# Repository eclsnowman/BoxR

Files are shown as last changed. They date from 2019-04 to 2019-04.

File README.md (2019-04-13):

# BoxR
BoxR 3D Printer by SMW3D aka Hobby-Fab (with Eric Lien)

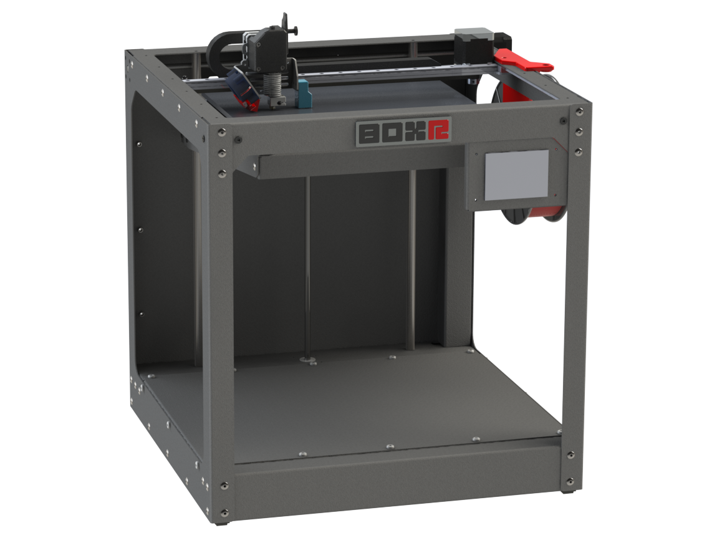
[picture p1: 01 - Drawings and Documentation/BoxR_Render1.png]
BoxR-3DP Render Image1


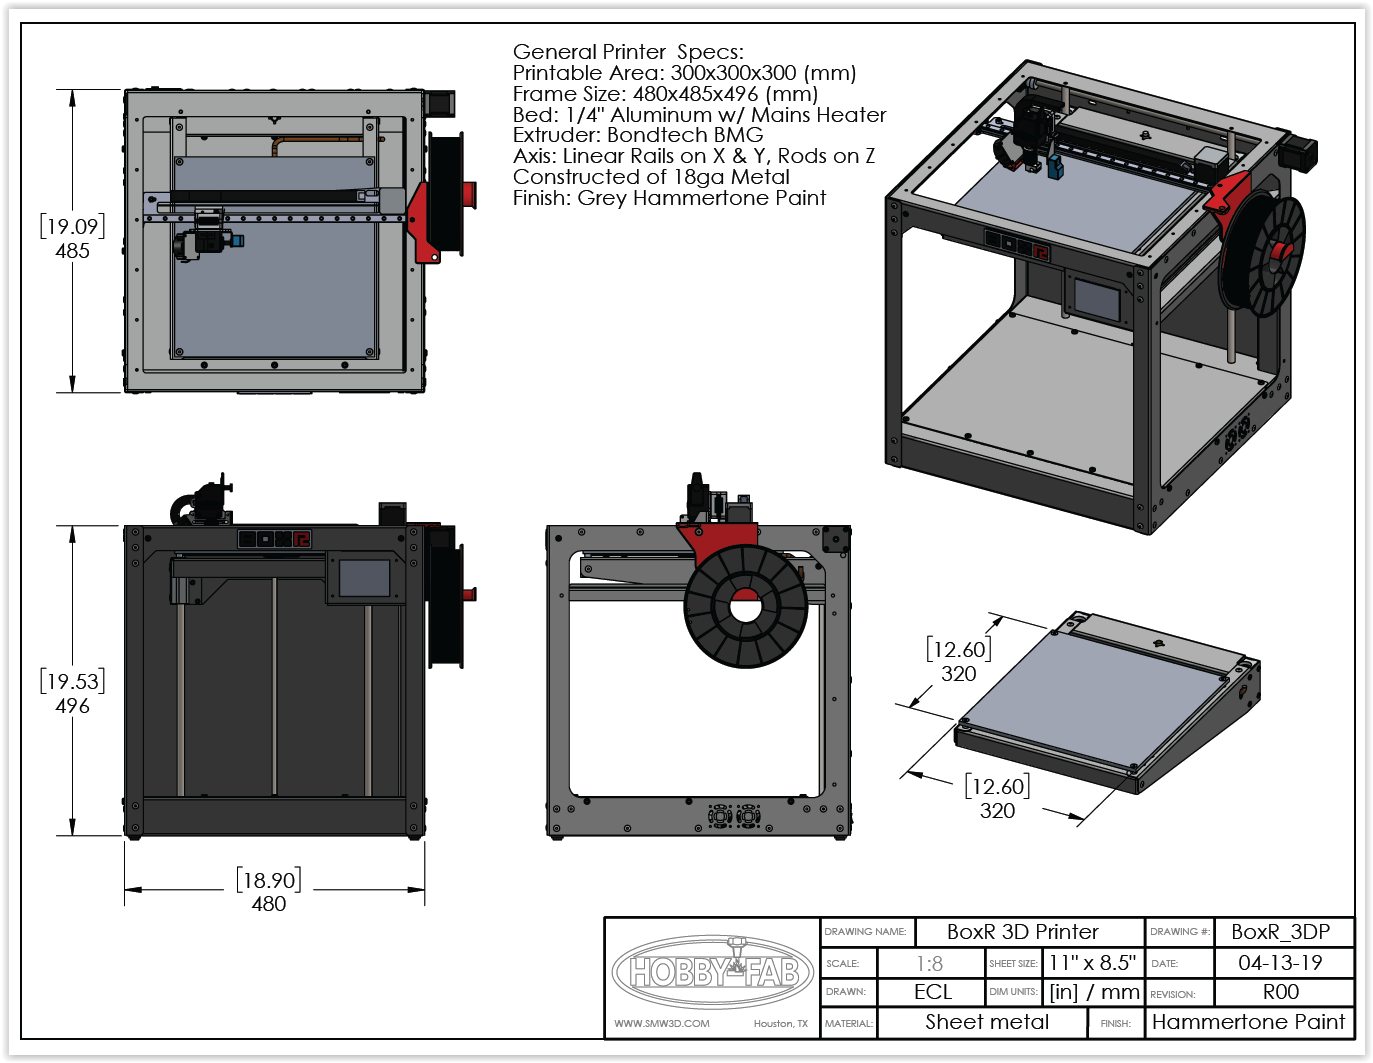
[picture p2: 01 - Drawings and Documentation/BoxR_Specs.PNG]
BoxR-3DP Specs


The BoxR 3D Printer is a larger format (300mm x 300mm x 300mm) cartesian x/y gantry printer with a moving z-axis bed. The BoxR printer was a project that Brandon Satterfield and I worked on together. Originally it was intended as a possible product line he could sell under his SMW3D / Hobby-Fab business. I have had the pleasure of knowing Brandon Satterfield for many years through the now defunct Google+. Over those years I have been fortunate enough to work on several cool project with Brandon and the team at SMW3D. Alas the advent of the CR-10, Ender3, and similar low cost reasonable quality Chinese printers that put the skids on this project. There are only two of these printers currently in the wild. I have one, and Brandon Satterfield has the other. Perhaps you might be the next?

On a sad note: due to the Chinese market spurring the race to the bottom on maker parts, kits, and printers it drove Brandon and his team on to greener pastures with the closure of Hobbyfab in 2019. But I am delighted to announce that Brandon has given me the OK to release the designs and plans on many of the cool machines we developed together out here on Github. The files here are my best attempt to cleanup and document with detailed 3D models the BoxR 3D printer as we left off on the project. I still use my BoxR Printer regularly, and actually had it out at MRRF the last few years. It is a capable and reliable 3D printer. If you have interest in building one, all the details to get you started should be available in this Github.

I have the 3D model files saved in several formats. I work in Solidworks natively, but I have also exported the model into Fusion360, X_T, Step, 3D-PDF. In addition I have generated DXF files for the 2D Panels which could be formed at a local sheet metal fabrication house by a potential maker looking to replicate the design. The BoxR design was my first for endeavor into sheet metal modeling in Solidworks. I have since improved my skills in this area, but I feel it is not too bad for a first attempt :)

I would like to end this by saying Brandon and his group over the years did amazing work for the community. They sponsored projects to many makers via at cost or free components to develop cool projects. They were always available to answer questions to potential makers on the kits and projects they sold (day or night). The maker community lost something special with the closure of SMW3D/Hobby-Fab. But the impact they left on the maker community will live on.

Thank you Brandon and team. You are amazing. And I am glad to have been but a small part in your chapter of the Maker Revolution story.

-Eric Lien

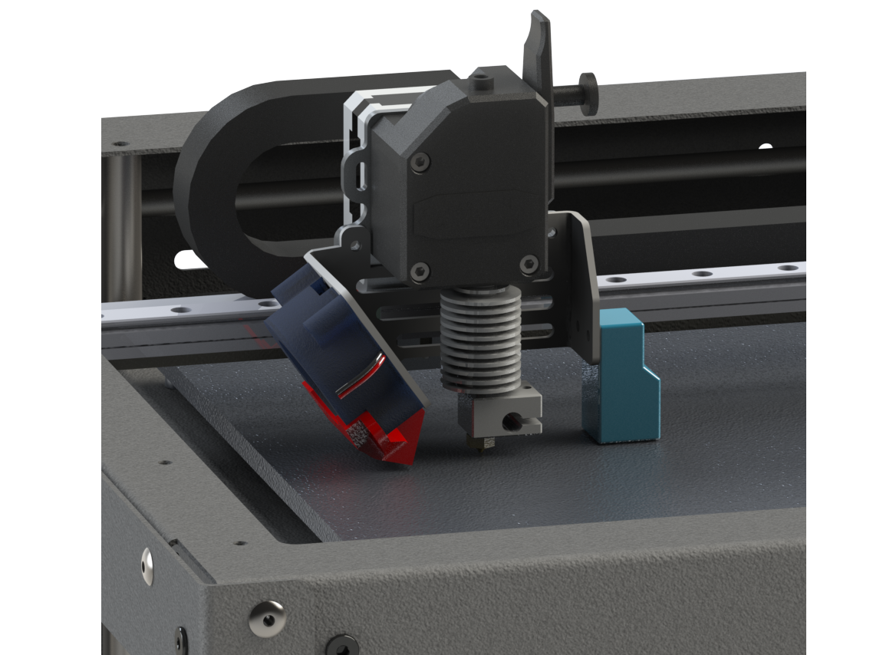
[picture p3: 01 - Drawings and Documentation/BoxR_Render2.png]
BoxR-3DP Render Image2


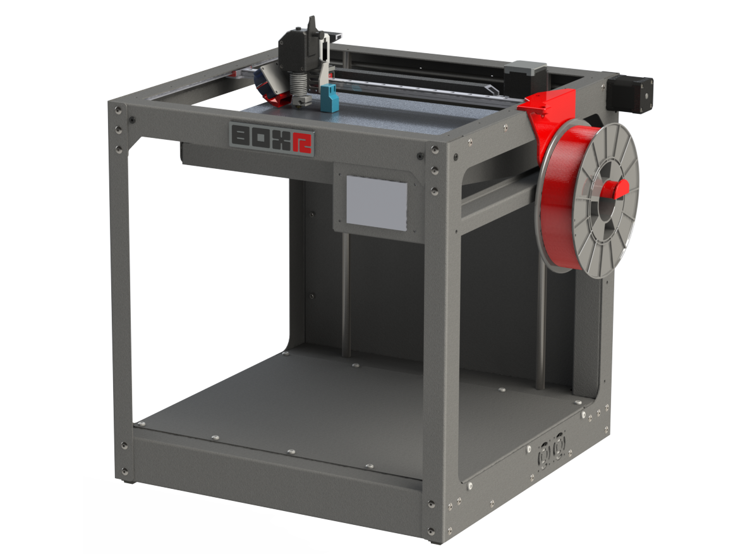
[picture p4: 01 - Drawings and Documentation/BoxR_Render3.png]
BoxR-3DP Render Image3


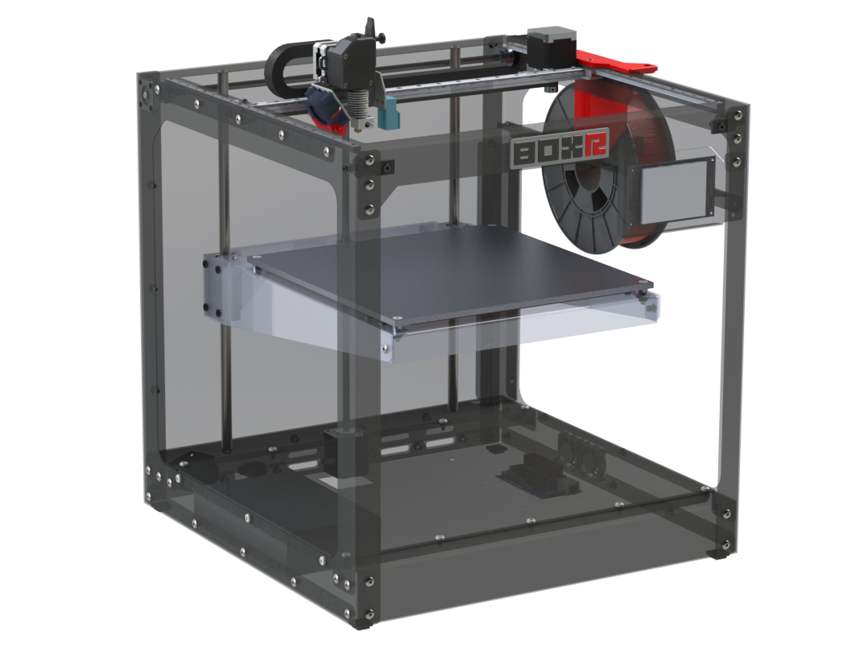
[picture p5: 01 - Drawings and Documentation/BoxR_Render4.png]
BoxR-3DP Render Image4


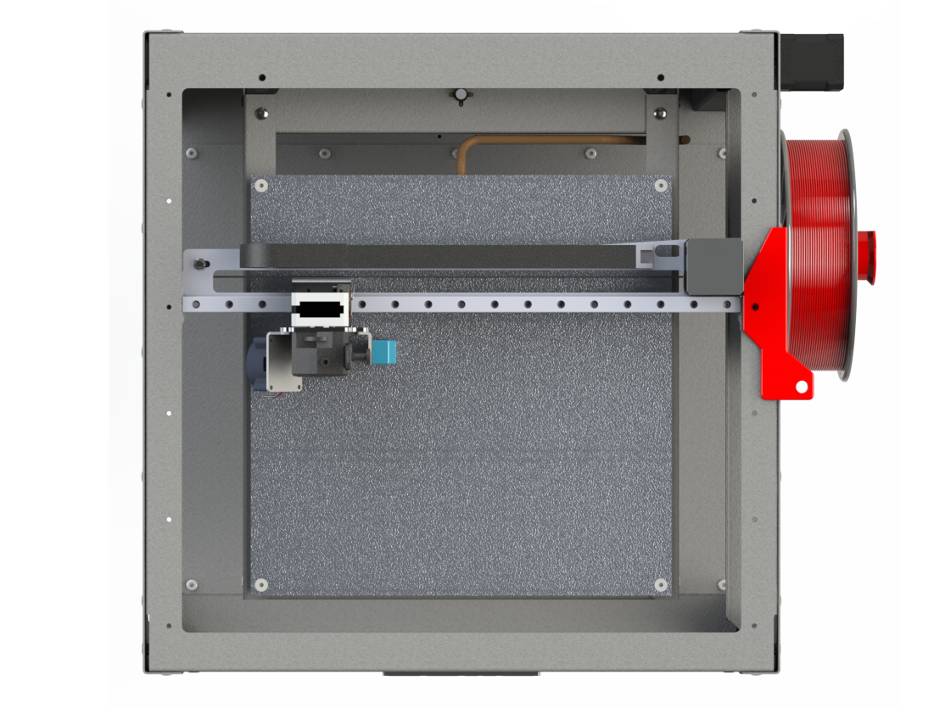
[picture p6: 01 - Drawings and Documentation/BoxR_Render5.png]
BoxR-3DP Render Image5


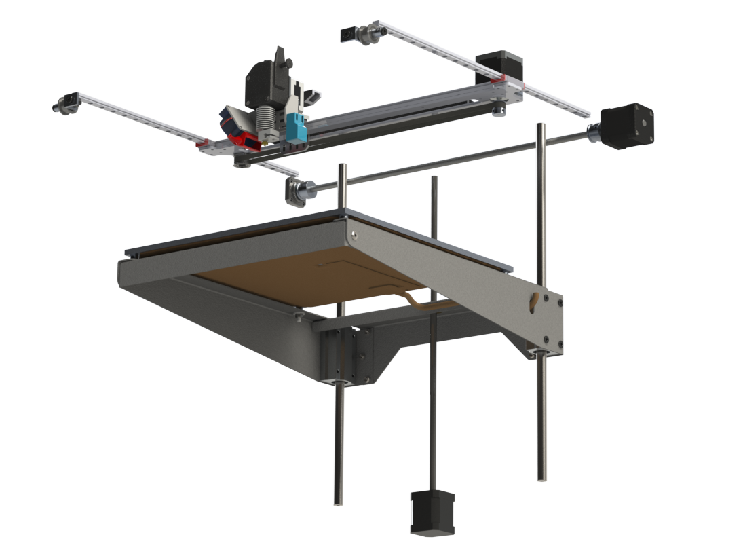
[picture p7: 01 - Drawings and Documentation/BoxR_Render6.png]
BoxR-3DP Render Image6


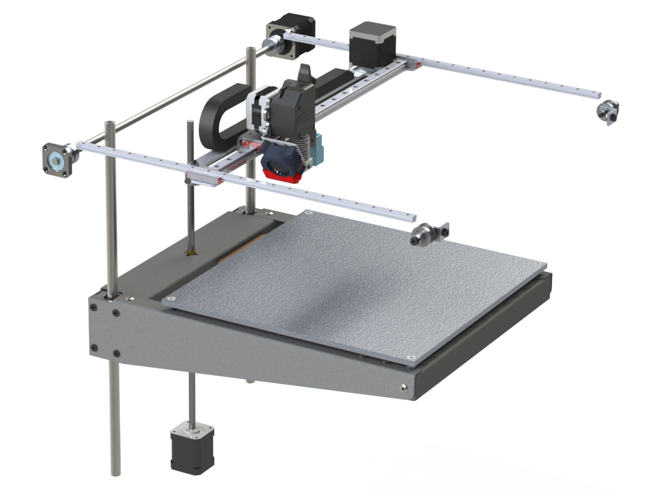
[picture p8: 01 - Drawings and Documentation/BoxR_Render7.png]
BoxR-3DP Render Image7


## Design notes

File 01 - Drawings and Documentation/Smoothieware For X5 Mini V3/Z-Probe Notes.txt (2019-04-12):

Okay so in the smoothieware docs on zprobes it states that a zprobe is not an endstop and cannot be used to home the z axis. But it can.

So I defined it as follows:
gamma_min_endstop                            1.29!^            #
#gamma_max_endstop                           1.28!^            #
gamma_homing_direction                       home_to_min       #
gamma_min                                    0                #
gamma_max                                    183              #

#probe endstop
#probe_pin                                   1.29!^            # optional pin for probe

# optional Z probe
zprobe.enable                                true           # set to true to enable a zprobe
zprobe.probe_pin                             1.29!^          # pin probe is attached to if NC remove the !
zprobe.slow_feedrate                         10               # mm/sec probe feed rate
zprobe.debounce_ms                           1             # set if noisy
zprobe.fast_feedrate                         100             # move feedrate mm/sec
zprobe.probe_height                          5               # how much above bed to start probe

The gamma (Z) endstop pin is 1.29 which is the ramps z_min_endstop, it is also defined as a zprobe, the ! after it reverses the probe logic i.e. equivalent to true enstop logic in Marlin.

I then home using 
G28 x
G28 Y
G1 X135 Y100 (middle of my 270x200 bed)
G28 Z

Then probe using whichever probing strategy such as grid levelling I have defined.

You can use your probe as z_min_endstop for homing and probing.

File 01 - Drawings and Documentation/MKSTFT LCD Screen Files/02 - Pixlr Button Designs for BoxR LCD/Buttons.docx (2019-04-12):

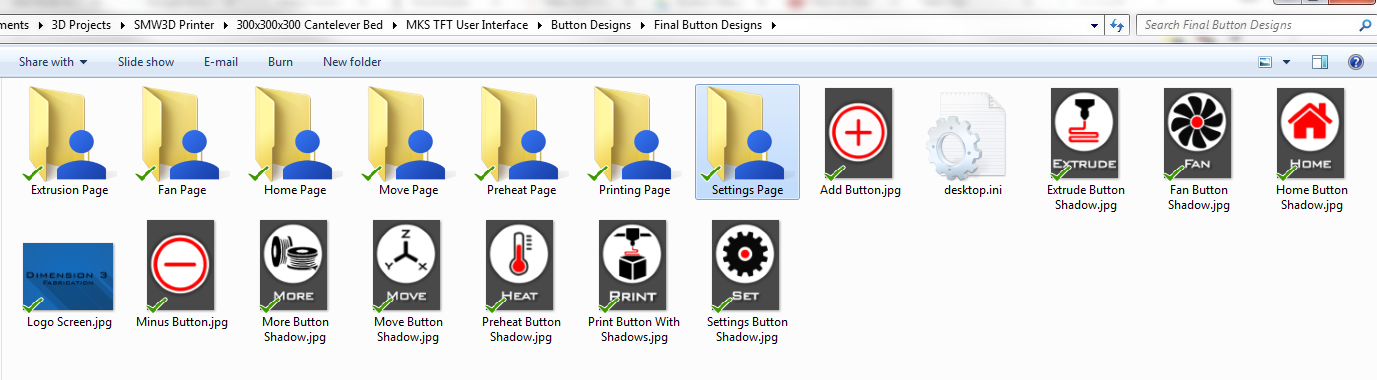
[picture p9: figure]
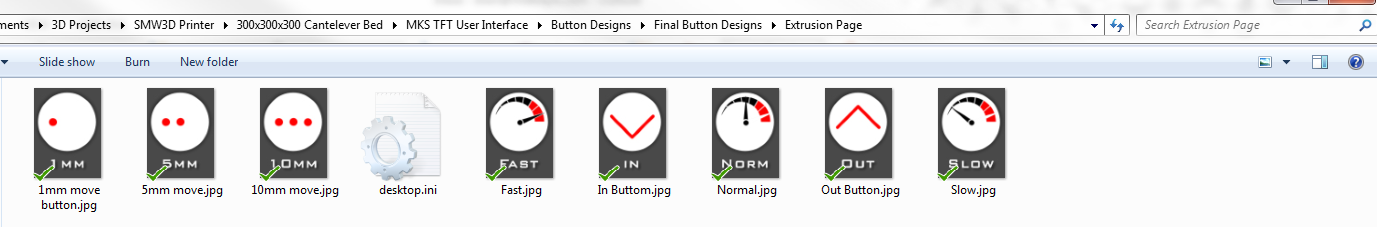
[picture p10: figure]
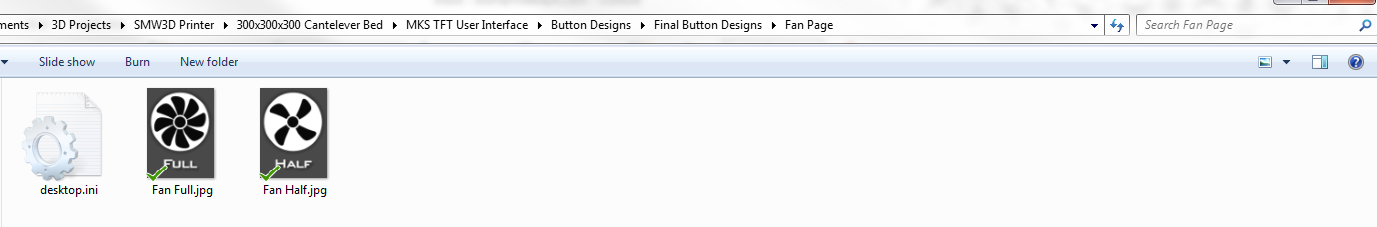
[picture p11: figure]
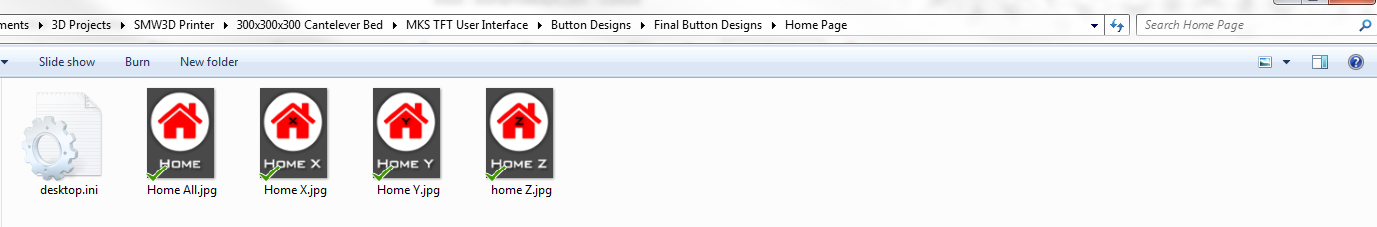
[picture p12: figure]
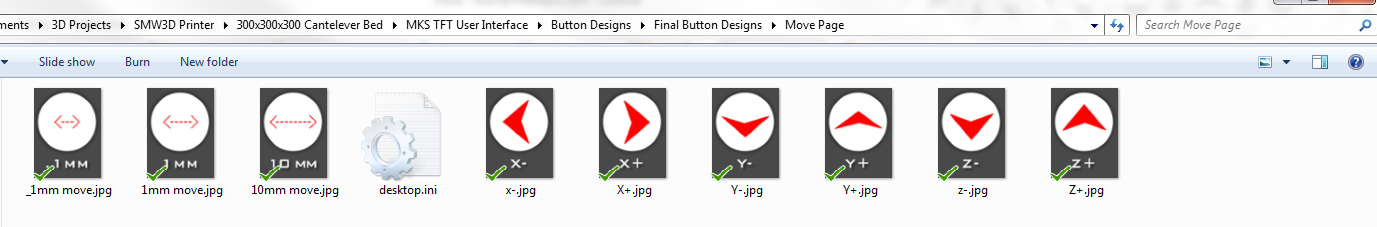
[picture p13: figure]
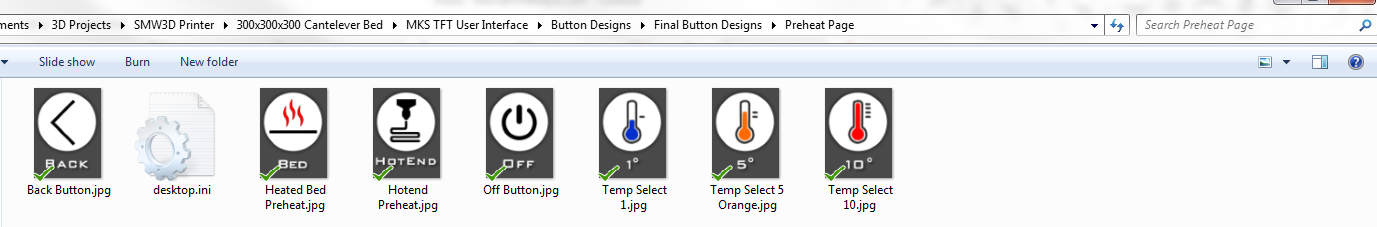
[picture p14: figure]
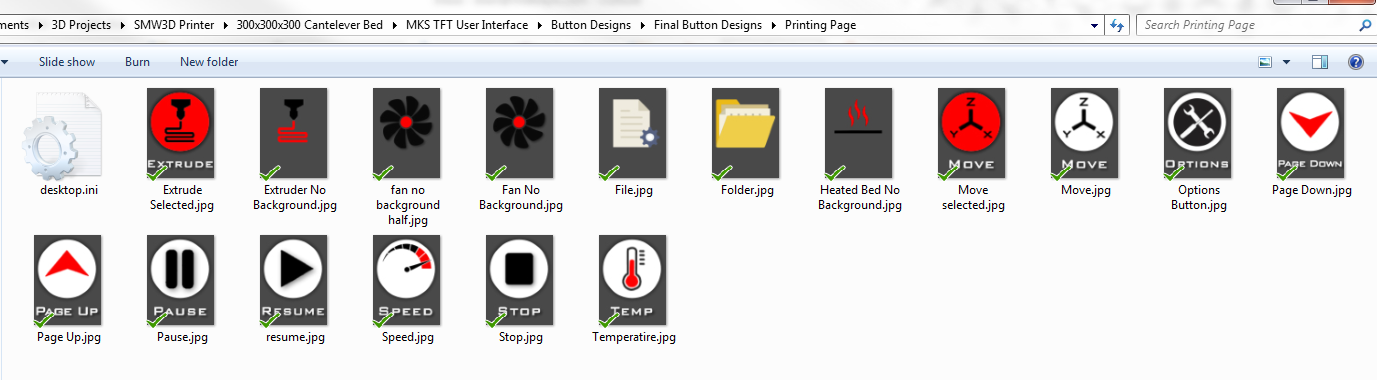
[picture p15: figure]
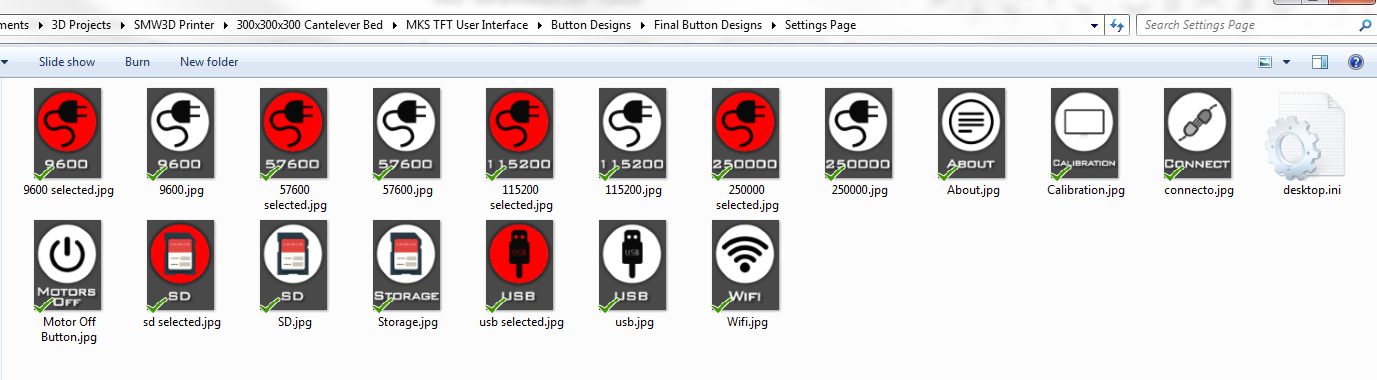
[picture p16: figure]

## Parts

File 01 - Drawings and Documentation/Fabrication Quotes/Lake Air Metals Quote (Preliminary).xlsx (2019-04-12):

Quantity | U/M | Unit Price | Lot Total | Summary of all parts by O.Q.
Bed Support 16ga Steel |  |  |  | QTY | Parts Total Cost
1 | EA | $151.61 | $151.61 | 1 | $1241.50
5 | EA | $39.28 | $196.40 | 5 | $321.14
10 | EA | $25.24 | $252.40 | 10 | $206.10
25 | EA | $16.82 | $420.50 | 25 | $137.07
50 | EA | $14.01 | $700.50 | 50 | $114.08
100 | EA | $12.60 | $1260.00 | 100 | $102.56
200 | EA | $11.90 | $2380.00 | 200 | $96.81
Frame Left 16ga Steel
1 | EA | $134.25 | $134.25
5 | EA | $36.22 | $181.10
10 | EA | $23.97 | $239.70
25 | EA | $16.62 | $415.50
50 | EA | $14.17 | $708.50
100 | EA | $12.94 | $1294.00
200 | EA | $12.33 | $2466.00
Frame Right 16ga Steel
1 | EA | $133.98 | $133.98
5 | EA | $35.95 | $179.75
10 | EA | $23.69 | $236.90
25 | EA | $16.34 | $408.50
50 | EA | $13.89 | $694.50
100 | EA | $12.67 | $1267.00
200 | EA | $12.05 | $2410.00
Top/Back 16GA Steel
1 | EA | $191.33 | $191.33
5 | EA | $58.20 | $291.00
10 | EA | $41.56 | $415.60
25 | EA | $31.57 | $789.25
50 | EA | $28.25 | $1412.50
100 | EA | $26.58 | $2658.00
200 | EA | $25.75 | $5150.00
Floor 16ga Steel
1 | EA | $182.79 | $182.79
5 | EA | $49.66 | $248.30
10 | EA | $33.02 | $330.20
25 | EA | $23.03 | $575.75
50 | EA | $19.71 | $985.50
100 | EA | $18.04 | $1804.00
200 | EA | $17.21 | $3442.00
Part Cooling Fan Mount 16ga Steel
1 | EA | $150.71 | $150.71
5 | EA | $32.93 | $164.65
10 | EA | $18.21 | $182.10
25 | EA | $9.38 | $234.50
50 | EA | $6.43 | $321.50
100 | EA | $4.96 | $496.00
200 | EA | $4.23 | $846.00
X-Axis Support 1/8" Aluminum
1 | EA | $152.47 | $152.47
5 | EA | $37.38 | $186.90
10 | EA | $23.00 | $230.00
25 | EA | $14.36 | $359.00
50 | EA | $11.49 | $574.50
100 | EA | $10.05 | $1005.00
200 | EA | $9.33 | $1866.00
Extruder Carriage Mount 1/8" Aluminum
1 | EA | $144.36 | $144.36
5 | EA | $31.52 | $157.60
10 | EA | $17.41 | $174.10
25 | EA | $8.95 | $223.75
50 | EA | $6.13 | $306.50
100 | EA | $4.72 | $472.00
200 | EA | $4.01 | $802.00

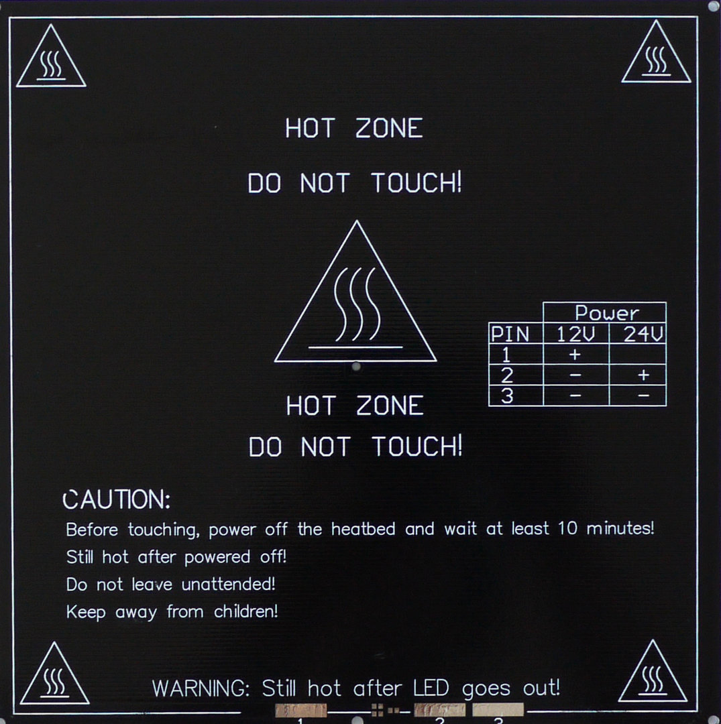
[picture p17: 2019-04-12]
03 - Other Variations/300x300x300 Side Supported/Components/Decals/ALU_PCB_MK3.jpg

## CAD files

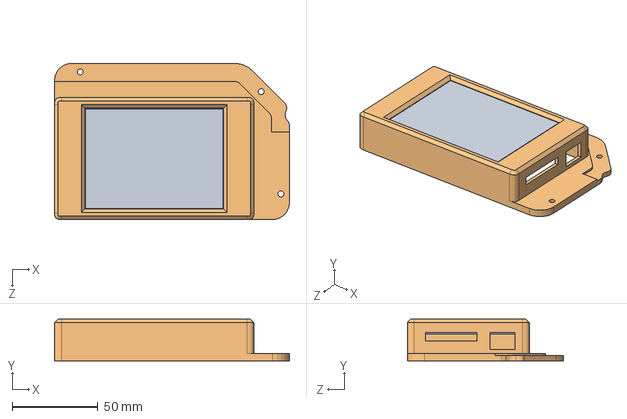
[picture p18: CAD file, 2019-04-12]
00 - Solidworks 3D/MKS TFT User Interface/Misc Media/SMW_MKS_TFT_ASMB_R3.SLDASM
136.9 x 24.3 x 91.1 mm
MKS_TFT_R3
Printed LCD Cover 2_R3

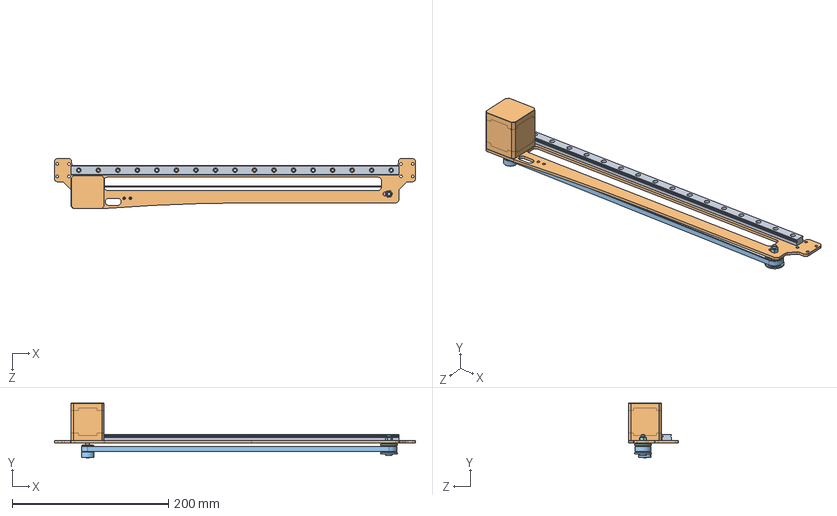
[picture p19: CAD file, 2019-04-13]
00 - Solidworks 3D/SubAsmb/X Axis Rail_Support_and_Drive_R3.sldasm
462.5 x 70.0 x 64.2 mm
MGNR12R_X-Axis_R3
Nema17-1704HS168A_R3
GT2 20T x 5mm_R3
Smooth Idler Pulley Wheel_R3
Ball Bearing 5 x 16 x 5_R3 x 2
Nylon Spacer 0.125in_R3
Precision Shim 8 x 5 x 1_R3
Nylon Insert Lock Nut M5_R3
Low Profile Screw M5_R3
X_Axis_Aluminum_Support_V3
X Axis GT2 Belt V3

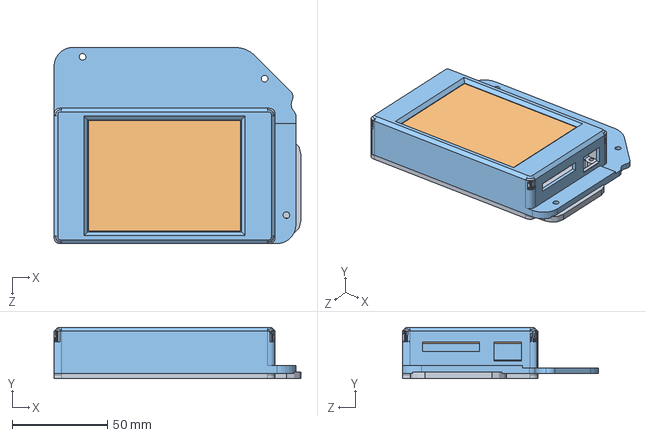
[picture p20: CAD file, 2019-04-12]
01 - Drawings and Documentation/MKSTFT LCD Screen Files/03 - Making Icons/Misc Media/SMW_MKS_TFT_ASMB.SLDASM
129.8 x 27.0 x 103.1 mm
MKS_TFT
Printed LCD Cover 2

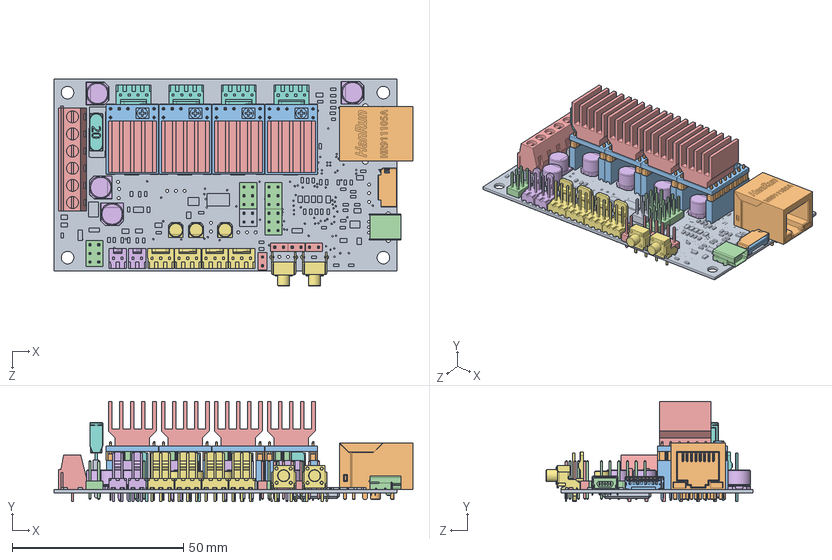
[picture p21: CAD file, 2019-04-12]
03 - Other Variations/300x300x300 Side Supported/Components/X5miniV3/X5miniV3.SLDASM
104.7 x 29.2 x 60.3 mm
x5mv3 Board
User Library-HR911105A
female_header_a-bl254-eg-g08d x 8
2x3 Mhdr x 8
tblock 6pin
2x2 Mhdr
pin_header_aw140-eg-g08d x 8
SD5984_PCB x 4
pin_header_aw140-eg-g02d x 4
Panucatt Heatsink x 4
female_header (3pin)_a-bl254-eg-g08d x 4
c-1825027-8-g1-3d x 2
MINI Blade Fuse Type 2
Fuse Holder
usb_a-usb_b-m5-c
2x1 Mhdr x 4
Capacitor1 x 8
Capacitor2 x 3

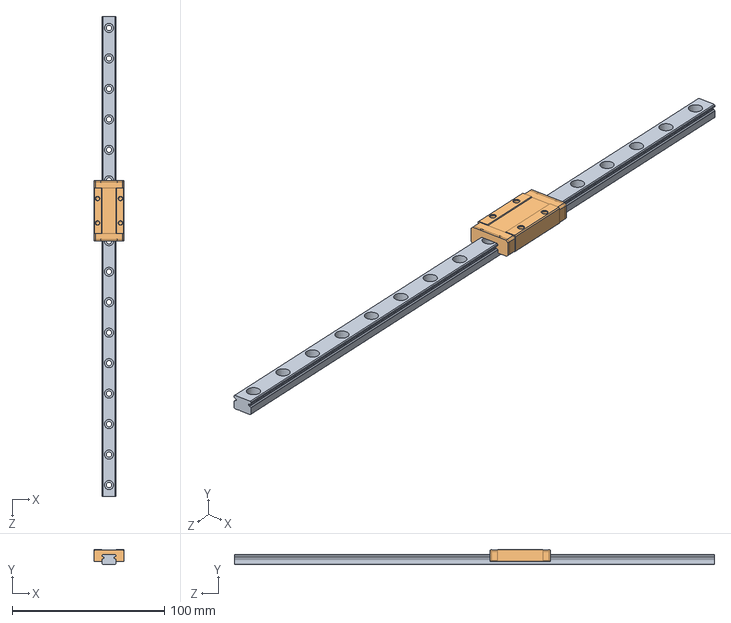
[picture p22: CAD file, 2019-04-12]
03 - Other Variations/300x300x300 Side Supported/SubAsmb/MGNR9R_with_MGN9HZFC_Carriage.SLDASM
20.0 x 10.0 x 315.0 mm
MGNR9R
MGN9HZFC_Carriage

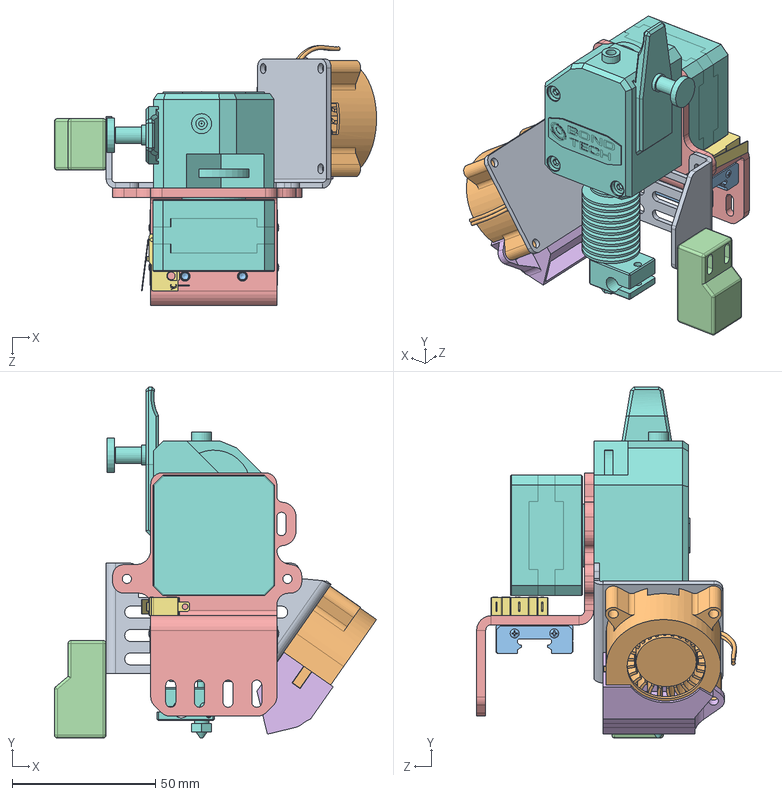
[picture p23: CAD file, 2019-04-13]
00 - Solidworks 3D/SubAsmb/Single Direct Drive Extruder_R3.sldasm
112.3 x 122.4 x 90.6 mm
Part Cooling Fan Mount_R3
4020Blower_R3
MGN12HZFC-HiwinCorporation-11-14-2016_R3
SN04_R3
Aluminum_Extruder_To_Carriage_Mount_R3
Part Cooling Fan V2_R3
Micro Switch Button_R3
BMG

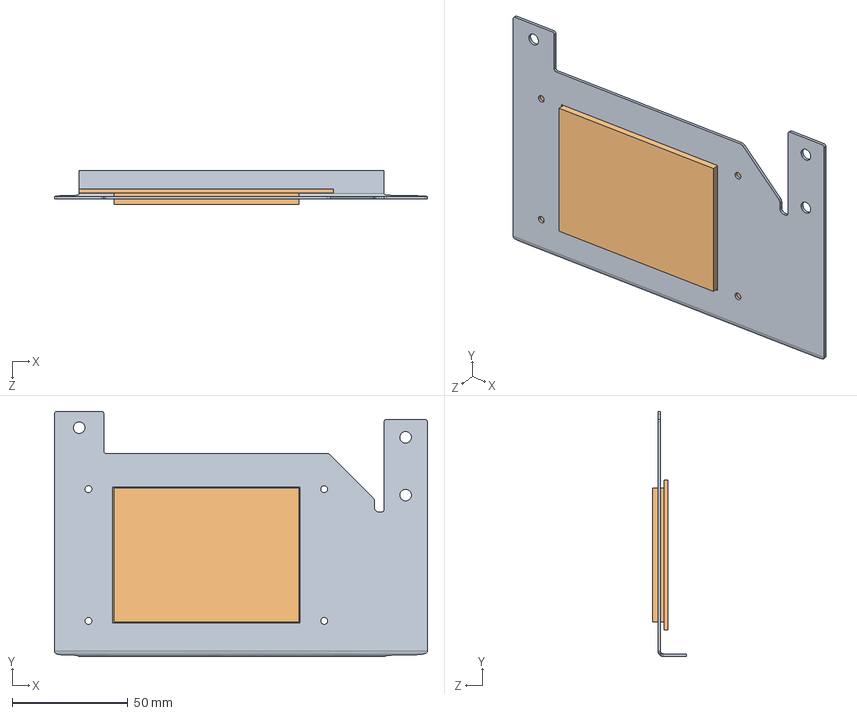
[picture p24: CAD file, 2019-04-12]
00 - Solidworks 3D/MKS TFT User Interface/Metal MKS TFT32 ASMB.SLDASM
161.4 x 106.0 x 14.7 mm
MKS TFT32 Display Mount
MKS_TFT_R3

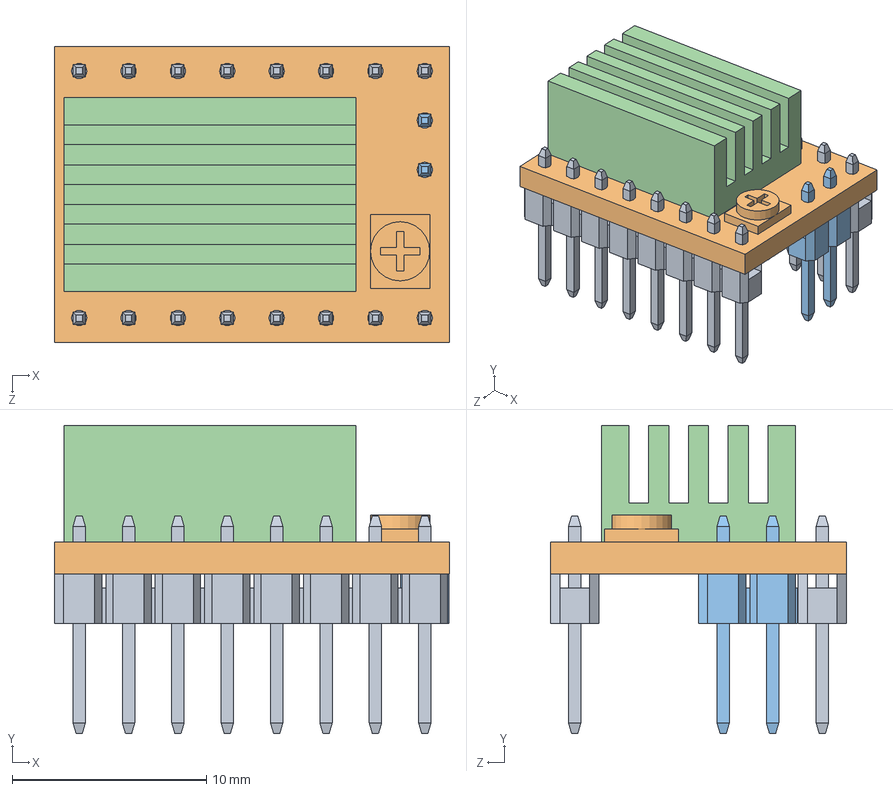
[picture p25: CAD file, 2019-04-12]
03 - Other Variations/300x300x300 Side Supported/Components/Geeetech_GT2560/Driver.SLDASM
20.3 x 15.9 x 15.2 mm
pin_header_aw140-eg-g08d x 2
SD5984_PCB
pin_header_aw140-eg-g02d
Heatsink

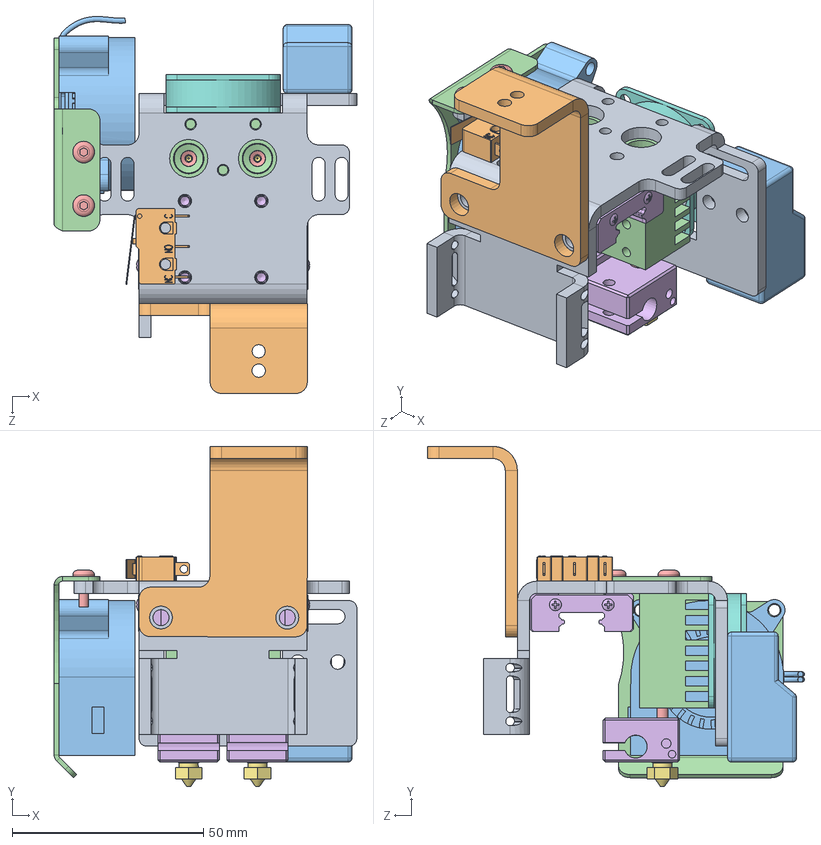
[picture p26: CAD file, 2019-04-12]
00 - Solidworks 3D/SubAsmb/Brandons Chimera Carriage.sldasm
79.2 x 89.1 x 98.6 mm
Aluminum_Chimera_Extruder_To_Carriage_Mount R3
Micro Switch Button_R3
SN04_R3
heat sink
heat break x 2
heater block x 2
0.4 nozzle x 2
Fan-House-30x30x10-Promoco(Fan-House-KDE0503PFB3-Promoco)
Fan-30x30x10-Promoco(Fan-KDE0503PFB3-Promoco)
Extruder_Carriage_Cable_Chain_Mount_R3
4020Blower_R3
RH_Fan gaurd
m3x8 x 2
MGN12HZFC-HiwinCorporation-11-14-2016_R3

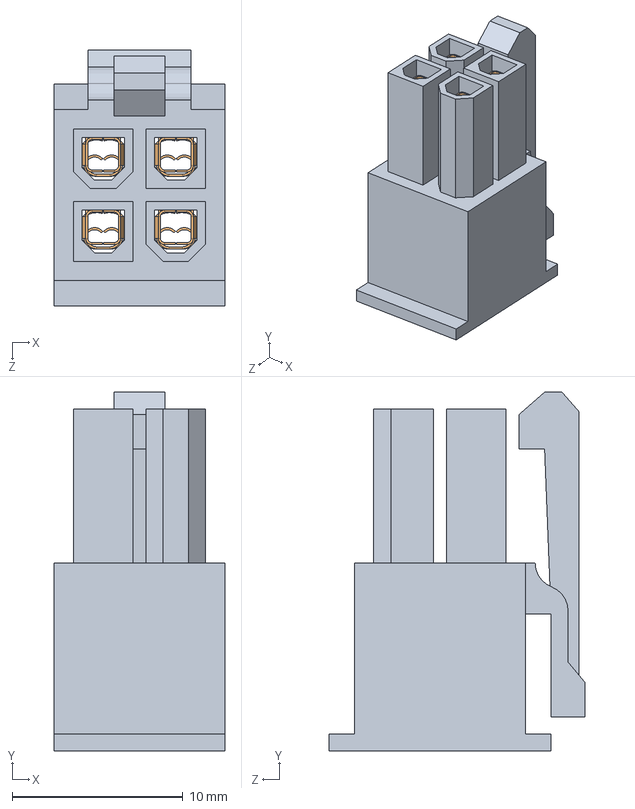
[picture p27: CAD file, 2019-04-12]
03 - Other Variations/300x300x300 Side Supported/Components/Geeetech_GT2560/ATX-12V-4-Pin.SLDASM
10.0 x 21.0 x 15.0 mm
ATX-12V-4-Pin-Body
ATX-Main-24-Pin-crimp x 4

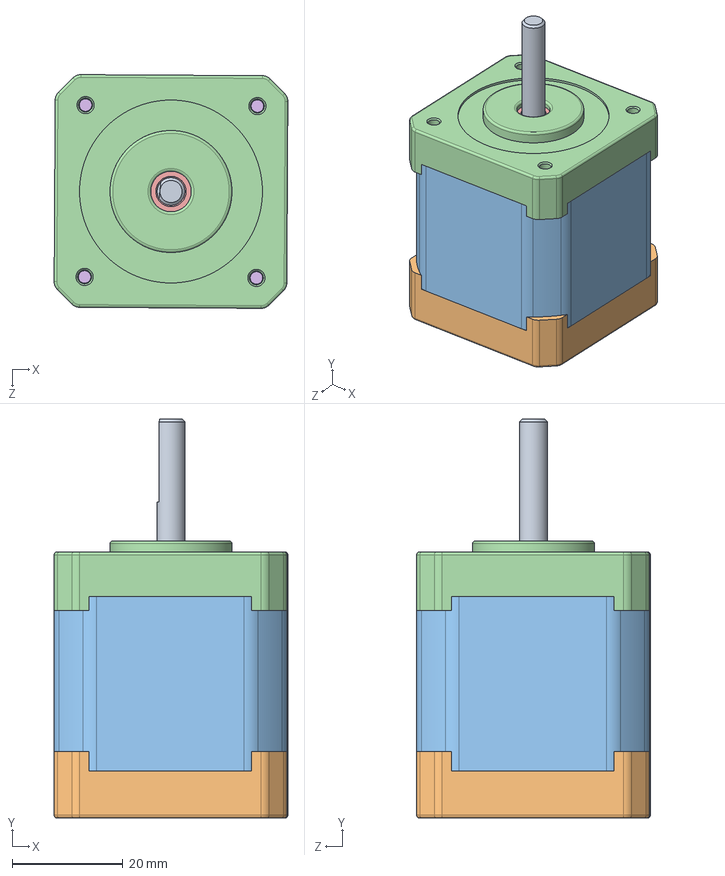
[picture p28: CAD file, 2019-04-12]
00 - Solidworks 3D/Components/1704HS168A/1704HS168A_R3[Conflict].SLDASM
42.2 x 72.0 x 42.2 mm
nema17_shaft_1704HS168A_R3
nema17_bottom_1704HS168A_R3
nema17_middle_1704HS168A_R3
nema17_top_1704HS168A_R3
6153K113_STAINLESS STEEL BALL BEARING x 2
91420A134_METRIC FLAT HEAD PHILLIPS MACHINE SCREW x 4

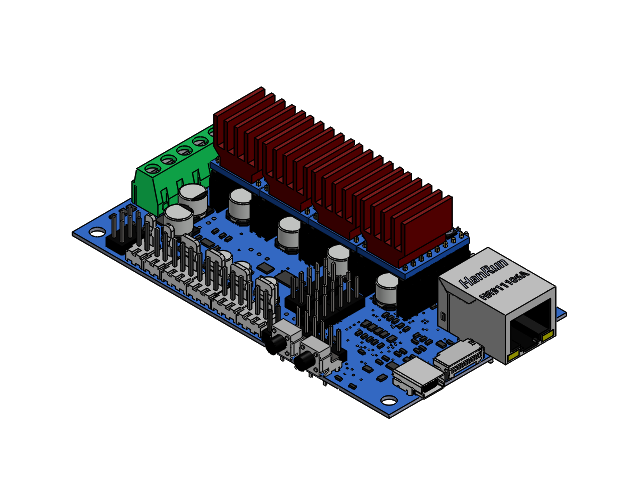
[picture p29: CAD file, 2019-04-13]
00 - Solidworks 3D/Components/X5miniV3/X5miniV3_R3.SLDASM
x5mv3 Board_R3
User Library-HR911105A_R3
female_header_a-bl254-eg-g08d_R3 x 8
2x3 Mhdr_R3 x 8
tblock 6pin_R3
Part6_R3 x 2
Part8_R3 x 4
Part10_R3 x 4
2x2 Mhdr_R3
pin_header_aw140-eg-g08d_R3 x 8
SD5984_PCB_R3 x 4
pin_header_aw140-eg-g02d_R3 x 4
Panucatt Heatsink_R3 x 4
female_header (3pin)_a-bl254-eg-g08d_R3 x 4
c-1825027-8-g1-3d_R3 x 2
MINI Blade Fuse Type 2_R3
Fuse Holder_R3
473093751_3_R3
473093751_1_2_R3
usb_a-usb_b-m5-c_R3
2x1 Mhdr_R3 x 4
Capacitor1_R3 x 8
Capacitor2_R3 x 3

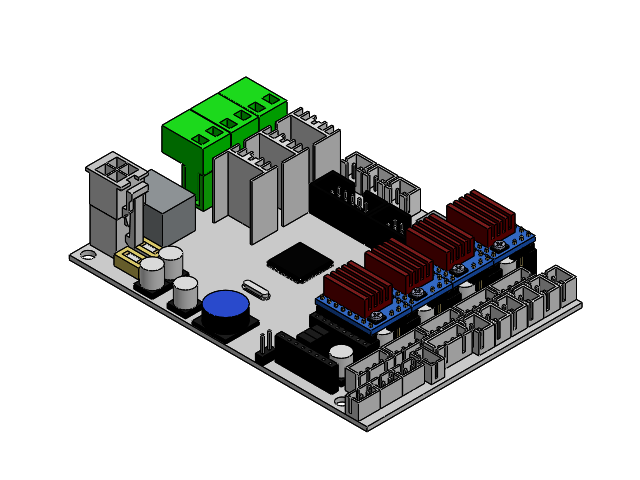
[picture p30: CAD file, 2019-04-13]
00 - Solidworks 3D/Components/Geeetech_GT2560/Geetech_GT2560_R3.SLDASM
Geetech_GT2560_R3
Geetech_GT2560 90deg Plug_R3 x 3
ATX-12V-4-Pin-Body_R3
ATX-Main-24-Pin-crimp_R3 x 4
pin_header_aw140-eg-g08d_R3 x 8
SD5984_PCB_R3 x 4
pin_header_aw140-eg-g02d_R3 x 4
Heatsink_R3 x 4

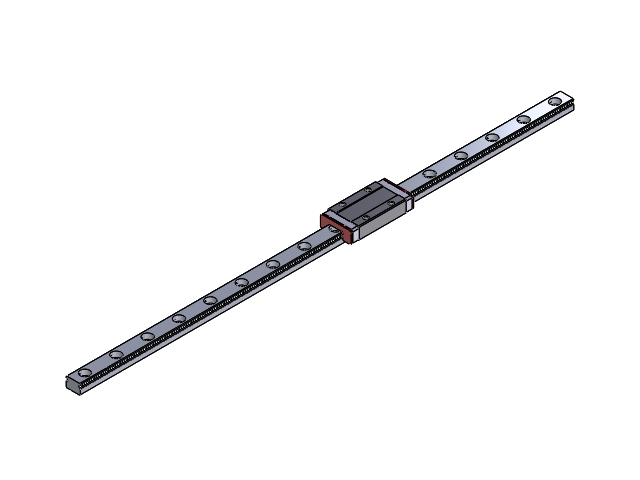
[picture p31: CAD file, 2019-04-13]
00 - Solidworks 3D/SubAsmb/MGNR9R_with_MGN9HZFC_Carriage_R3.SLDASM
MGNR9R_R3
MGN9HZFC_Carriage_R3

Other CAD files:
00 - Solidworks 3D/Components/Geeetech_GT2560/ATX-Main-24-Pin-crimp_R3.sldprt
00 - Solidworks 3D/Components/Jamicon_KF0410-01_R3.SLDASM
00 - Solidworks 3D/Components/Geeetech_GT2560/Driver_R3.SLDASM
00 - Solidworks 3D/Components/X5miniV3/Components/Panucatt SD5984_R3.SLDASM
00 - Solidworks 3D/Components/0.4 nozzle.SLDPRT
00 - Solidworks 3D/Components/1704HS168A/6153K113_STAINLESS STEEL BALL BEARING.SLDPRT
00 - Solidworks 3D/Components/1704HS168A/91420A134_METRIC FLAT HEAD PHILLIPS MACHINE SCREW.SLDPRT
00 - Solidworks 3D/Components/1704HS168A/nema17_bottom_1704HS168A_R3.SLDPRT
00 - Solidworks 3D/Components/1704HS168A/nema17_middle_1704HS168A_R3.SLDPRT
00 - Solidworks 3D/Components/1704HS168A/nema17_shaft_1704HS168A_R3.SLDPRT
00 - Solidworks 3D/Components/1704HS168A/nema17_top_1704HS168A_R3.SLDPRT
00 - Solidworks 3D/Components/4020Blower_R3.SLDPRT
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

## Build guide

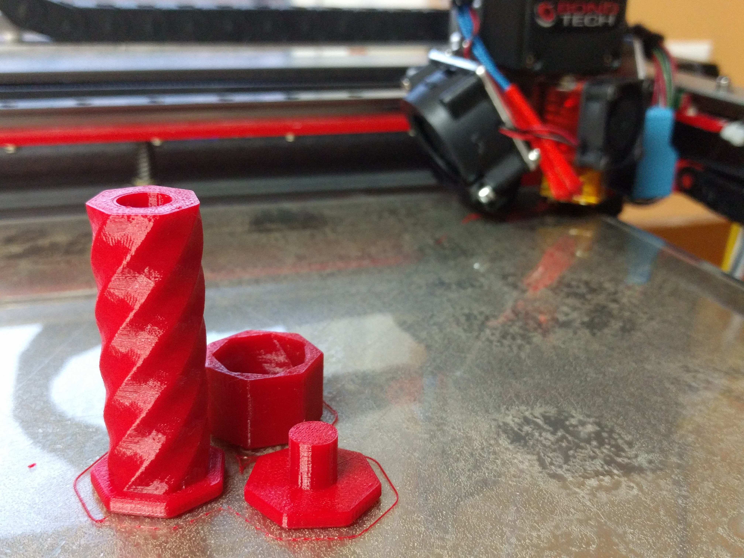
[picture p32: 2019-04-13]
01 - Drawings and Documentation/BoxR_Print_Examples (7).jpg

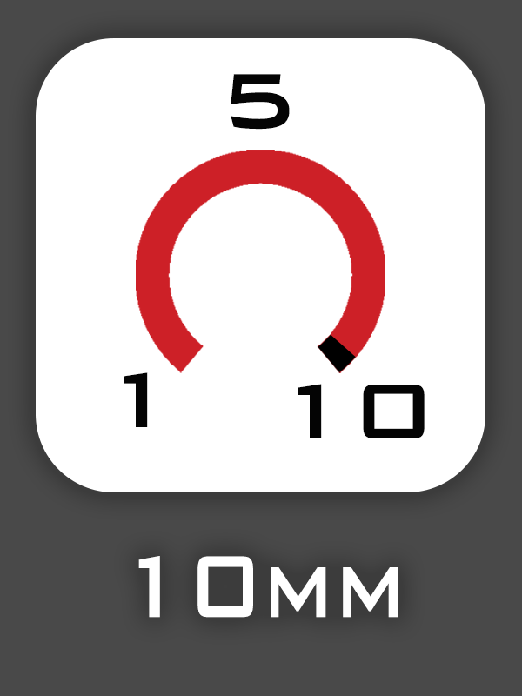
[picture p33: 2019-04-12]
01 - Drawings and Documentation/MKSTFT LCD Screen Files/01 - SMW3D Photoshop/Buttons/600x800 Button Masters/bmp_step10_mm.bmp

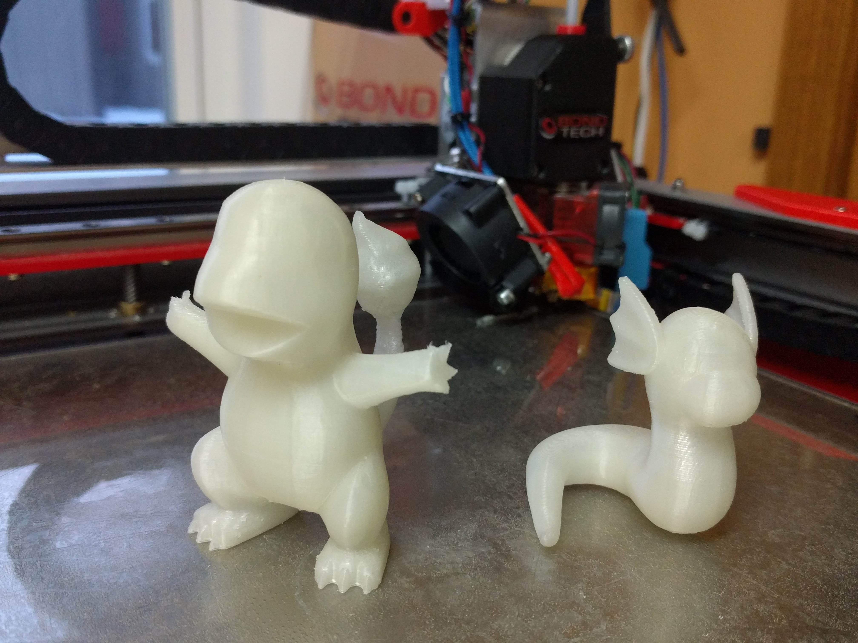
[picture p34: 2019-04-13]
01 - Drawings and Documentation/BoxR_Print_Examples (10).jpg

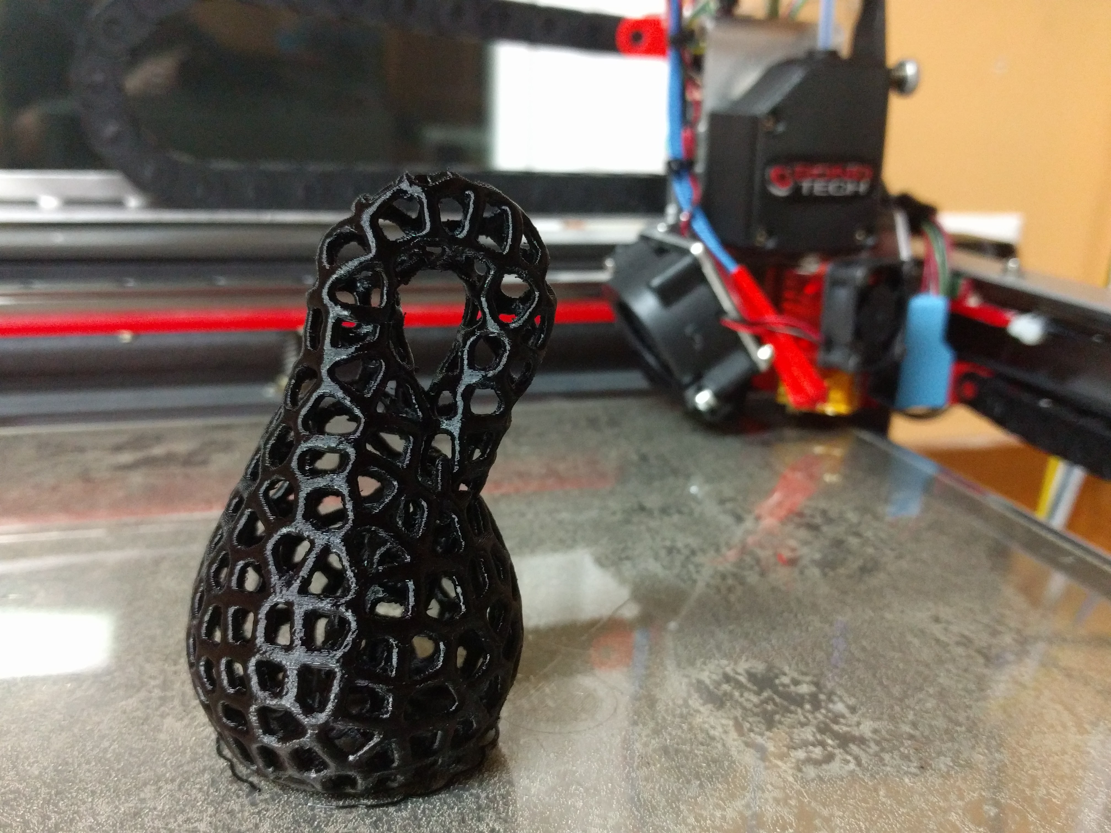
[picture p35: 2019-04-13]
01 - Drawings and Documentation/BoxR_Print_Examples (6).jpg

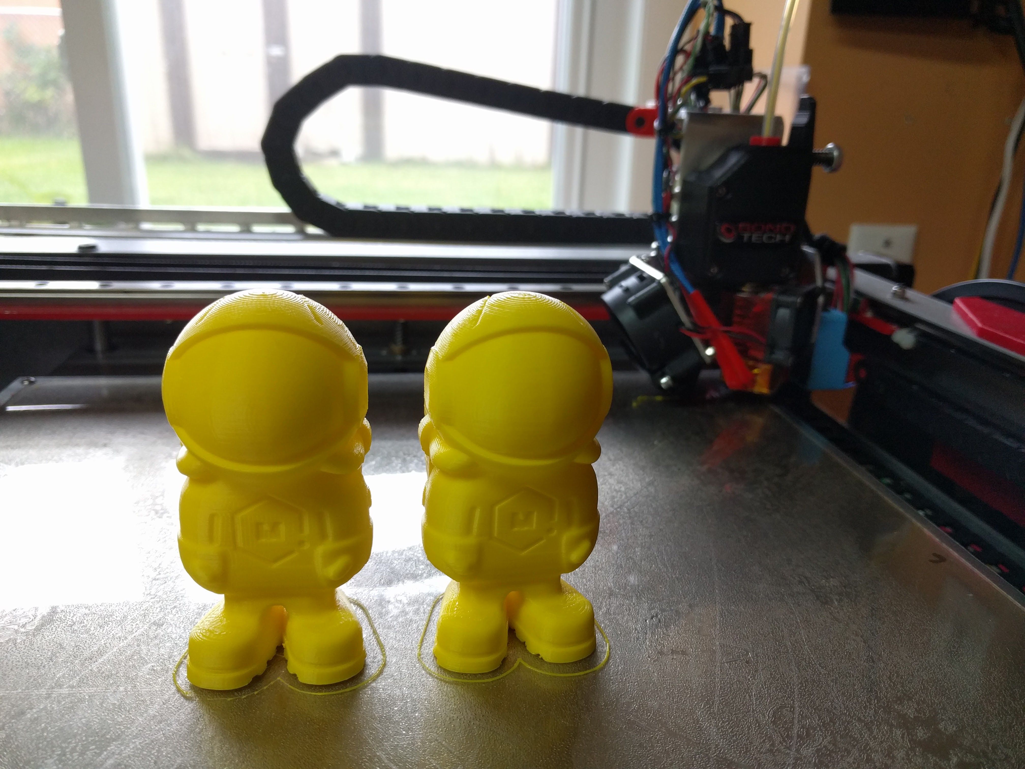
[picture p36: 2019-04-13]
01 - Drawings and Documentation/BoxR_Print_Examples (9).jpg

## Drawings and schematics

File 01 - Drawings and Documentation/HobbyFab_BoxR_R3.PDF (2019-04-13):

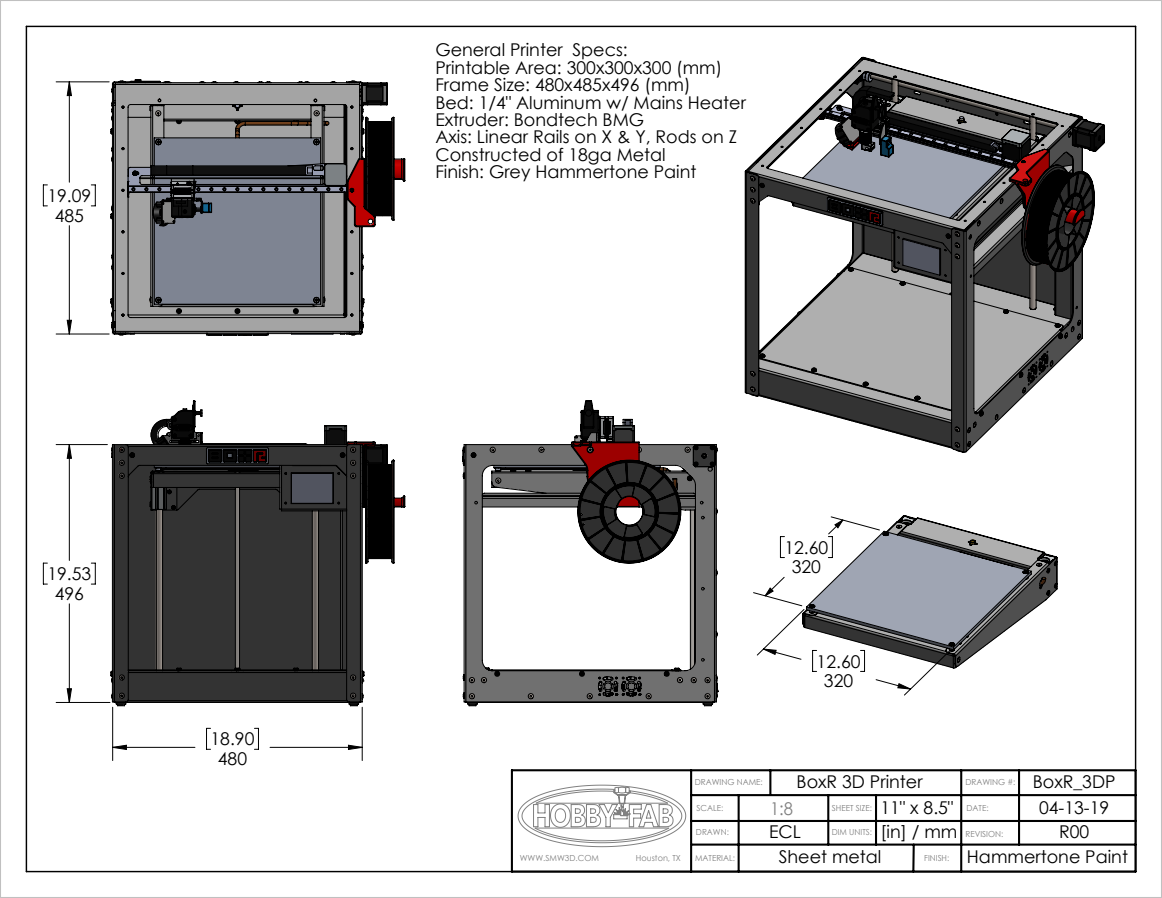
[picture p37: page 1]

General Printer Specs:
Printable Area: 300x300x300 (mm)
Frame Size: 480x485x496 (mm)
Bed: 1/4" Aluminum w/ Mains Heater
Extruder: Bondtech BMG
Axis: Linear Rails on X & Y, Rods on Z
Constructed of 18ga Metal
Finish: Grey Hammertone Paint

WWW.SMW3D.COM Houston, TX | DRAWING NAME: | BoxR 3D Printer | DRAWING #: | BoxR_3DP

SCALE: | 1:8 | SHEET SIZE: | 11" x 8.5" | DATE: | 04-13-19
DRAWN: | ECL | DIM UNITS: | [in] / mm | REVISION: | R00

MATERIAL: | Sheet metal | FINISH: | Hammertone Paint

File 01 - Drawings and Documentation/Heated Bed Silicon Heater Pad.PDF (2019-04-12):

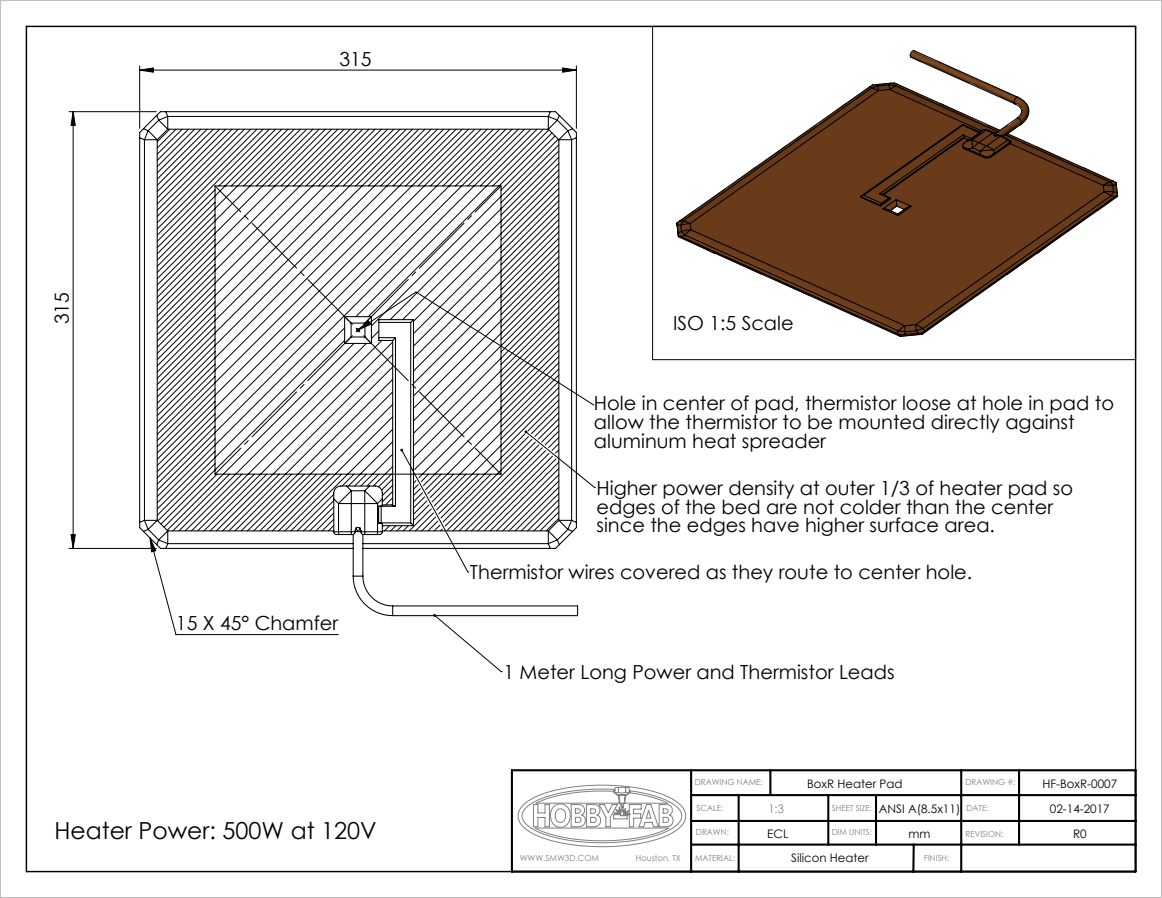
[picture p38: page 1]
15 X 45° Chamfer; ISO 1:5 Scale

Hole in center of pad, thermistor loose at hole in pad to
allow the thermistor to be mounted directly against
aluminum heat spreader
Higher power density at outer 1/3 of heater pad so
edges of the bed are not colder than the center
since the edges have higher surface area.

Thermistor wires covered as they route to center hole.

1 Meter Long Power and Thermistor Leads

WWW.SMW3D.COM Houston, TX | DRAWING NAME: | BoxR Heater Pad | DRAWING #: | HF-BoxR-0007

SCALE: | 1:3 | SHEET SIZE: | ANSI A(8.5x11) | DATE: | 02-14-2017
DRAWN: | ECL | DIM UNITS: | mm | REVISION: | R0

Heater Power: 500W at 120V

MATERIAL: | Silicon Heater | FINISH:

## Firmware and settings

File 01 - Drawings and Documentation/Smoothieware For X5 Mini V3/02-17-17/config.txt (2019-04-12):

# Robot module configurations : general handling of movement G-codes and slicing into moves
default_feed_rate                            4000             # Default rate ( mm/minute ) for G1/G2/G3 moves
default_seek_rate                            4000             # Default rate ( mm/minute ) for G0 moves
mm_per_arc_segment                           0.5              # Arcs are cut into segments ( lines ), this is the length for these segments.  Smaller values mean more resolution, higher values mean faster computation
#mm_per_line_segment                          5                # Lines can be cut into segments ( not usefull with cartesian coordinates robots ).

# Arm solution configuration : Cartesian robot. Translates mm positions into stepper positions
alpha_steps_per_mm                           160               # Steps per mm for alpha stepper
beta_steps_per_mm                            100               # Steps per mm for beta stepper
gamma_steps_per_mm                           800        # Steps per mm for gamma stepper

# Planner module configuration : Look-ahead and acceleration configuration
planner_queue_size                           32               # DO NOT CHANGE THIS UNLESS YOU KNOW EXACTLY WHAT YOUR ARE DOING
acceleration                                 2000             # Acceleration in mm/second/second.
z_acceleration                               500              # Acceleration for Z only moves in mm/s^2, 0 disables it, disabled by default. DO NOT SET ON A DELTA
junction_deviation                           0.025             # Similar to the old "max_jerk", in millimeters, see : https://github.com/grbl/grbl/blob/master/planner.c#L409
                                                              # and https://github.com/grbl/grbl/wiki/Configuring-Grbl-v0.8 . Lower values mean being more careful, higher values means being faster and have more jerk
z_junction_deviation                         0                # Disable Jerk for Z

# Stepper module configuration
microseconds_per_step_pulse                  1                # Duration of step pulses to stepper drivers, in microseconds
base_stepping_frequency                      100000           # Base frequency for stepping

# Stepper module pins ( ports, and pin numbers, appending "!" to the number will invert a pin )
alpha_step_pin                               2.1              # Pin for alpha stepper step signal
alpha_dir_pin                                0.11             # Pin for alpha stepper direction
alpha_en_pin                                 0.10            # Pin for alpha enable pin
alpha_current                                1.30              # X stepper motor current
x_axis_max_speed                             30000            # mm/min
alpha_max_rate                               30000.0          # mm/min actuator max speed

beta_step_pin                                2.2              # Pin for beta stepper step signal
beta_dir_pin                                 0.20             # Pin for beta stepper direction
beta_en_pin                                  0.19            # Pin for beta enable
beta_current                                 1.45              # Y stepper motor current
y_axis_max_speed                             30000            # mm/min
beta_max_rate                                30000.0          # mm/min actuator max speed

gamma_step_pin                               2.3              # Pin for gamma stepper step signal
gamma_dir_pin                                0.22             # Pin for gamma stepper direction
gamma_en_pin                                 0.21            # Pin for gamma enable
gamma_current                                1.35              # Z stepper motor current
z_axis_max_speed                             1200              # mm/min
gamma_max_rate                               1200.0            # mm/min actuator max speed

# Serial communications configuration ( baud rate default to 9600 if undefined )
uart0.baud_rate                              250000           # Baud rate for the default hardware serial port
second_usb_serial_enable                     false            # This enables a second usb serial port (to have both pronterface and a terminal connected)

#msd_disable                                 false            # disable the MSD (USB SDCARD) when set to true
#leds_disable                                true             # disable using leds after config loaded
#dfu_enable                                  false            # for linux developers, set to true to enable DFU
#watchdog_timeout                            10               # watchdog timeout in seconds, default is 10, set to 0 to disable the watchdog


## Extruder module configuration
extruder.hotend.enable                          true             # Whether to activate the extruder module at all. All configuration is ignored if false
extruder.hotend.steps_per_mm                    837              # Steps per mm for extruder stepper
extruder.hotend.default_feed_rate               600              # Default rate ( mm/minute ) for moves where only the extruder moves
extruder.hotend.acceleration                    1000             # Acceleration for the stepper motor mm/sec²
extruder.hotend.max_speed                       50               # mm/s

extruder.hotend.step_pin                        2.0              # Pin for extruder step signal
extruder.hotend.dir_pin                         0.5              # Pin for extruder dir signal
extruder.hotend.en_pin                          0.4              # Pin for extruder enable signal

delta_current                                1.0              # Extruder stepper motor current

# Laser module configuration
laser_module_enable                          false            # Whether to activate the laser module at all. All configuration is
                                                              # ignored if false.
#laser_module_pin                             2.5             # this pin will be PWMed to control the laser. Only P2.0 - P2.5, P1.18, P1.20, P1.21, P1.23, P1.24, P1.26, P3.25, P3.26
                                                              # can be used since laser requires hardware PWM
#laser_module_maximum_power                   1.0             # this is the maximum duty cycle that will be applied to the laser
#laser_module_minimum_power                   0.0             # This is a value just below the minimum duty cycle that keeps the laser
                                                              # active without actually burning.
#laser_module_default_power                   0.8             # This is the default laser power that will be used for cuts if a power has not been specified.  The value is a scale between
                                                              # the maximum and minimum power levels specified above
#laser_module_pwm_period                      20              # this sets the pwm frequency as the period in microseconds

# Hotend temperature control configuration
temperature_control.hotend.enable            true             # Whether to activate this ( "hotend" ) module at all. All configuration is ignored if false.
temperature_control.hotend.thermistor_pin    0.24             # Pin for the thermistor to read
temperature_control.hotend.heater_pin        2.5              # Pin that controls the heater
temperature_control.hotend.thermistor        Semitec          # see http://smoothieware.org/temperaturecontrol#toc5
#temperature_control.hotend.beta             4066             # or set the beta value

temperature_control.hotend.set_m_code        104              #
temperature_control.hotend.set_and_wait_m_code 109            #
temperature_control.hotend.designator        T                #
#temperature_control.hotend.max_temp         300              # Set maximum temperature - Will prevent heating above 300 by default
#temperature_control.hotend.min_temp         0                # Set minimum temperature - Will prevent heating below 0 by default

# safety control is enabled by default and can be overidden here, the values show the defaults
#temperature_control.hotend.runaway_heating_timeout      900   # max is 2040 seconds, how long it can take to heat up
#temperature_control.hotend.runaway_cooling_timeout        0   # max is 2040 seconds, how long it can take to cool down if temp is set lower
#temperature_control.hotend.runaway_range                20    # Max setting is 63°C

temperature_control.hotend.p_factor          57.8972            #
temperature_control.hotend.i_factor          5.3983             #
temperature_control.hotend.d_factor          155.2368           #
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

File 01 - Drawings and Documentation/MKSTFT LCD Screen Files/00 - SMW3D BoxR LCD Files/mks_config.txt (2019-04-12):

#mainboard firmware setting(marlin:1; repetier:2; smoothie:3)
>cfg_firmware_type:3

#machine setting (Normal:1; Delta:2)
>cfg_machine_type:1

#language (Simplified Chinese:1; traditional Chinese:2; English:3)
>cfg_language_type:3

#whether set machine auto-off after print finishes(auto-off:1; NO:0)
>cfg_print_finish_close_Machine:0

#pause position (-1 is invalid; Z-axis is relative position)
>cfg_XPOS:-1
>cfg_YPOS:-1
>cfg_ZADD:10

#extruder number(one:1; dual:2)
>cfg_sprayer_counter:1

#whether has heated bed(YES:1; NO: 0)
>cfg_custom_bed_flag:1

#the max target Temp of sprayer and heated bed
>cfg_max_sprayer_temperature:270
>cfg_max_hotbed_temperature:150

#the level signal of outage detection module PB1(low level:0; high level:1)
>cfg_PB0_PB1_Level:1

#wifi mode(AP:1; STA:2)
>cfg_wifi_mode:1

#wifi name and password
>cfg_wifi_ap_name:MKS_wifi
>cfg_wifi_key_code:makerbase

#Dynamic access IP
>cfg_ip_dhcp_flag:1

#IP/mask/gateway
>cfg_ip_address:192.168.3.100
>cfg_ip_mask:255.255.255.0
>cfg_ip_gate:192.168.3.1

#the color of screen background
>cfg_background_color:0x494949

#the color of title text
>cfg_title_color:0xFFFFFF

#the color of temperature,fan,(etc) background
>cfg_state_background_color:0x494949

#the color of temprature,fan,(etc) text
>cfg_state_text_color:0xFFFFFF

#the color of file button
>cfg_filename_background_color:0x494949

#the color of file text
>cfg_filename_color:0xFFFFFF

#the color of background in printing 
>cfg_printingstat_word_background_color:0x494949

#the color of text in printing status
>cfg_printingstat_word_color:0xFFFFFF

#3D effects setting (disable: 0; enable: 1)
>cfg_BUTTON_3D_effects:0

#the speed of filament replacing(mm/min)
>cfg_filament_change_speed:1200
#the length of filament replacing(mm)
>cfg_filament_change_step:5
#the min temperature of filament replacing
>cfg_filament_limit_temperature:175

#bed leveling setting(auto leveler:1; manual leveling:0)
>cfg_leveling_mode:0

#the coordinates of 4 point  on manual leveling
>cfg_point1:50,50
>cfg_point2:250,50
>cfg_point3:250,250
>cfg_point4:50,250

#the moving speed of leveling(mm/min)
>cfg_leveling_z_speed:1500
>cfg_leveling_xy_speed:3000

#user-defined function1 and 2.(whether display this button .  disable: 0; enable: 1)
>cfg_function_btn1_display:1
>cfg_function_btn2_display:1

#command of user-defined function
>function_btn1_cmd:M84;
>function_btn2_cmd:G28;G29;

#set number of  "More" button 
>moreitem_pic_cnt:2

#edit command for 1~7 "More" button,each command must be separated by semicolon ";"
>moreitem_button1_cmd:M306 Z0;

>moreitem_button2_cmd:M500;

>moreitem_button3_cmd:G28 Y0;

>moreitem_button4_cmd:G28 Y0;

>moreitem_button5_cmd:G28 Z0;

>moreitem_button6_cmd:G28 Z0;

>moreitem_button7_cmd:G28;

#how many "More" button show on screen interface
>morefunc_cnt:0

#command setting on button1~6
>morefunc1_cmd:G28;
>morefunc2_cmd:G28;
>morefunc3_cmd:G28;
>morefunc4_cmd:G28;
>morefunc5_cmd:G28;
>morefunc6_cmd:G28;

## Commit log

2019-04-12 Initial Upload
    Initial Upload
    [0.4 nozzle.SLDPRT, 1704HS168A_R3[Conflict].SLDASM, 2x1 Mhdr.sldprt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]
2019-04-13 Adding drawings and a few model tweaks.
    Adding drawings and a few model tweaks.
    [2x1 Mhdr_R3.sldprt, 2x2 Mhdr_R3.sldprt, 2x3 Mhdr_R3.sldprt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]
2019-04-13 Added Pictures and Print Videos
    Added Pictures and Print Videos
